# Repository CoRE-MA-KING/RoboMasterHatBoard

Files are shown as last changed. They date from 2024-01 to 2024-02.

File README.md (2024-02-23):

# RoboMasterHatBoard
ロボマス開発ボード用ハットです。  
CoREに出場するロボットに利用しているメインボードとして[RoboMaster 開発ボードタイプA](https://store.dji.com/jp/product/rm-development-board-type-a?vid=42041)を利用しているので、このボードから2024年大会用に必要なピンをコネクタにまとめるための基板です。

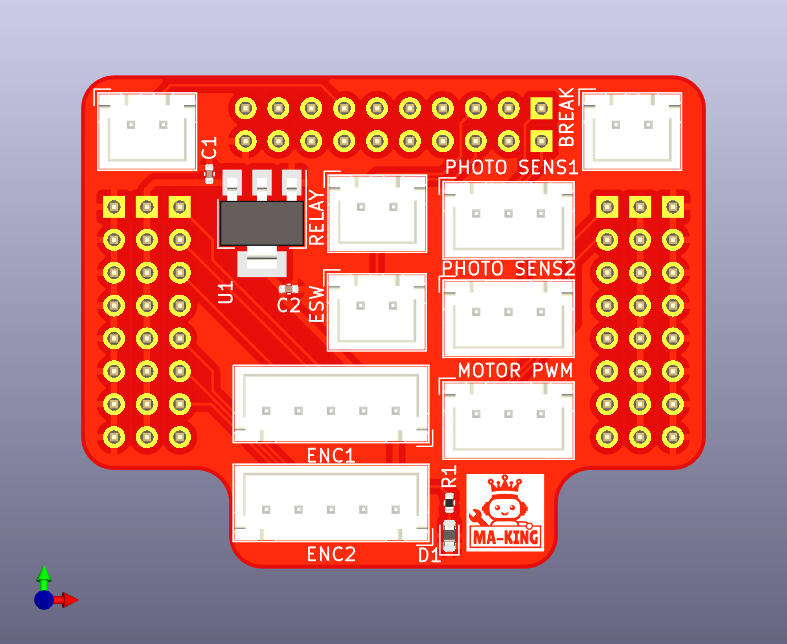
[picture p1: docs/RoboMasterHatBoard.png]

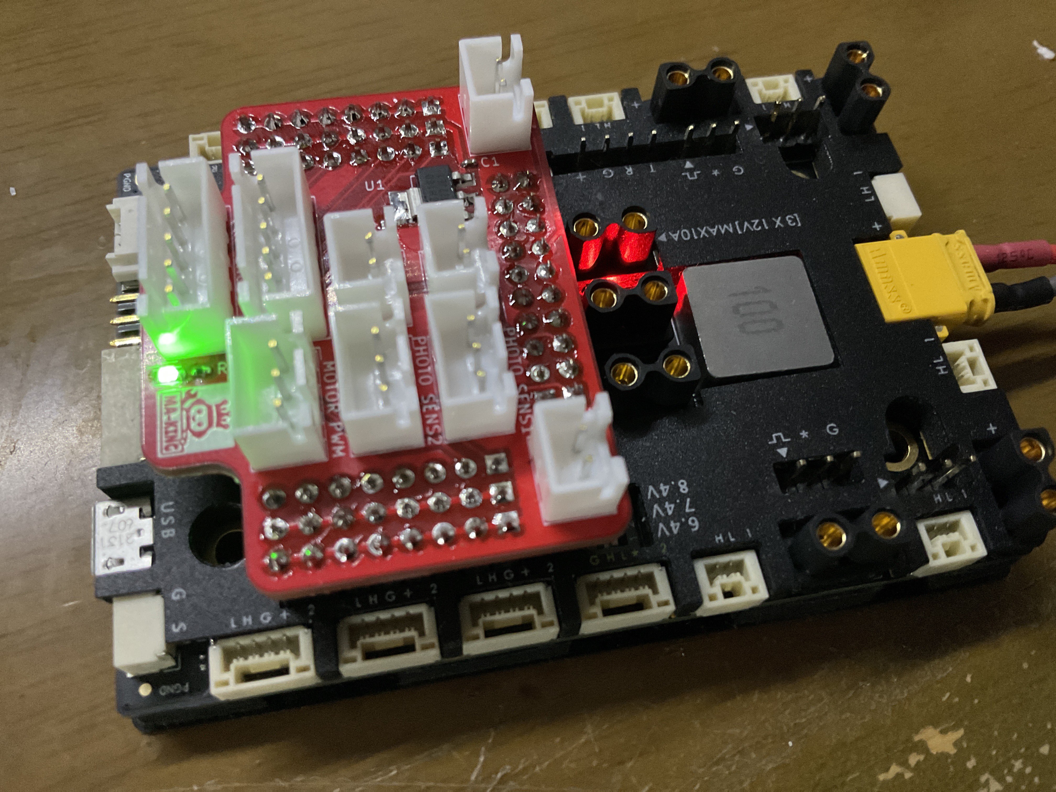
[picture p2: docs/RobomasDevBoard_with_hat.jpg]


# 機能
ロボマス開発ボードにはピンヘッダからいくつかのピンが出ているので、そこから今回のロボットで利用するピンを取り出します。

具体的に以下のピンを取り出します。
|ピン名|ペリフェラル|用途|備考|
|---|---|---|---|
|PD12|TIM4_CH1| モータ1PWM用||
|PD13|TIM4_CH2| モータ2PWM用||
|PA0|TIM2_CH1| エンコーダ1 A相||
|PA1|TIM2_CH2| エンコーダ1 B相||
|PA2|GPIO_INPUT| エンコーダ1 Z相||
|PI5|TIM8_CH1| エンコーダ2 A相||
|PI6|TIM8_CH2| エンコーダ2 B相||
|PI7|GPIO_INPUT| エンコーダ2 Z相||
|PF0|GPIO_INPUT|フォトインタラプタ1入力|マイコンの内部プルアップ必須|
|PF1|GPIO_INPUT|フォトインタラプタ2入力|マイコンの内部プルアップ必須|
|PE6|GPIO_INPUT|非常停止ボタン入力|マイコンの内部プルアップ必須|
|PE12|GPIO_OUTPUT|リレー駆動信号||
|PC3|GPIO_INPUT|撃破信号入力|PC3は5 Vトレラントなので5 V入力可能|
|PC1|GPIO|汎用GPIO|予備ポート 5 Vトレラントピン|

v0.1の基板上のシルクと回路図上の信号線が逆になっているので注意。回路図が間違っているということにして基板のシルクか上の表に従えばOK。

基板上のコネクタのピンアサインは次の通り
### MOTOR PWM
|1|2|3|
|---|---|---|
|TIM4_CH1(PD12)|TIM4_CH2(PD13)|GND|

### PHOTO SENS1
|1|2|3|
|---|---|---|
|5 V|INPUT(PF0)|GND|

### PHOTO SENS2
|1|2|3|
|---|---|---|
|5 V|INPUT(PF1)|GND|

### ENC1
|1|2|3|4|5|
|---|---|---|---|---|
|3.3 V|TIM2_CH1(PA1)|TIM2_CH2(PA2)|INPUT(PA2)|GND|

### ENC2
|1|2|3|4|5|
|---|---|---|---|---|
|3.3 V|TIM8_CH1(PI5)|TIM8_CH2(Pi6)|INPUT(PI7)|GND|

### RELAY
|1|2|
|---|---|
|OUTPUT(PE12)|GND|

### ESW
|1|2|
|---|---|
|INPUT(PE6)|GND|

### BREAK
|1|2|
|---|---|
|INPUT(PC3)|GND|

### 予備ポート
|1|2|
|---|---|
|INPUT(PC1)|GND|

## 参考
ロボマス開発ボードピンヘッダ部分のピンアサインは[回路図](https://ausdroid.co/wp-content/uploads/2020/08/RoboMaster-Development-Board-Type-A-Schematic.pdf)より
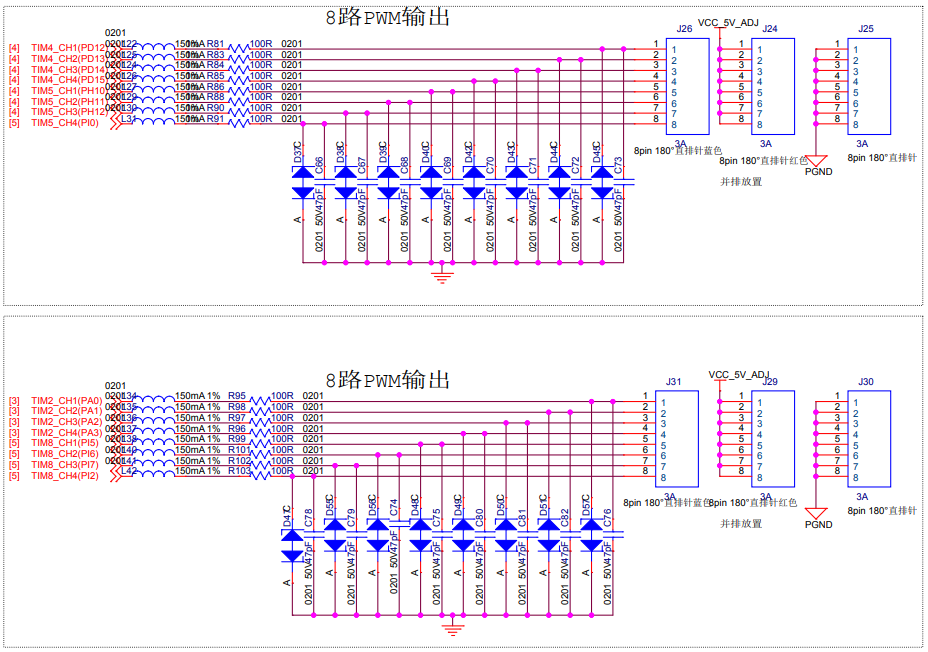
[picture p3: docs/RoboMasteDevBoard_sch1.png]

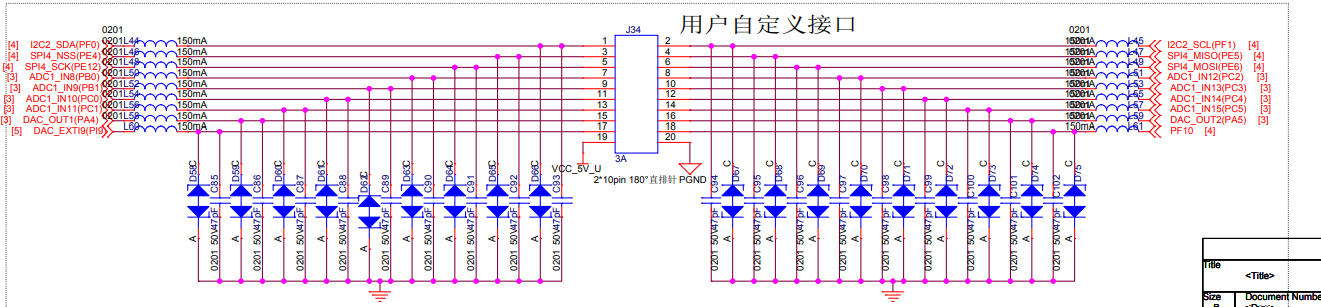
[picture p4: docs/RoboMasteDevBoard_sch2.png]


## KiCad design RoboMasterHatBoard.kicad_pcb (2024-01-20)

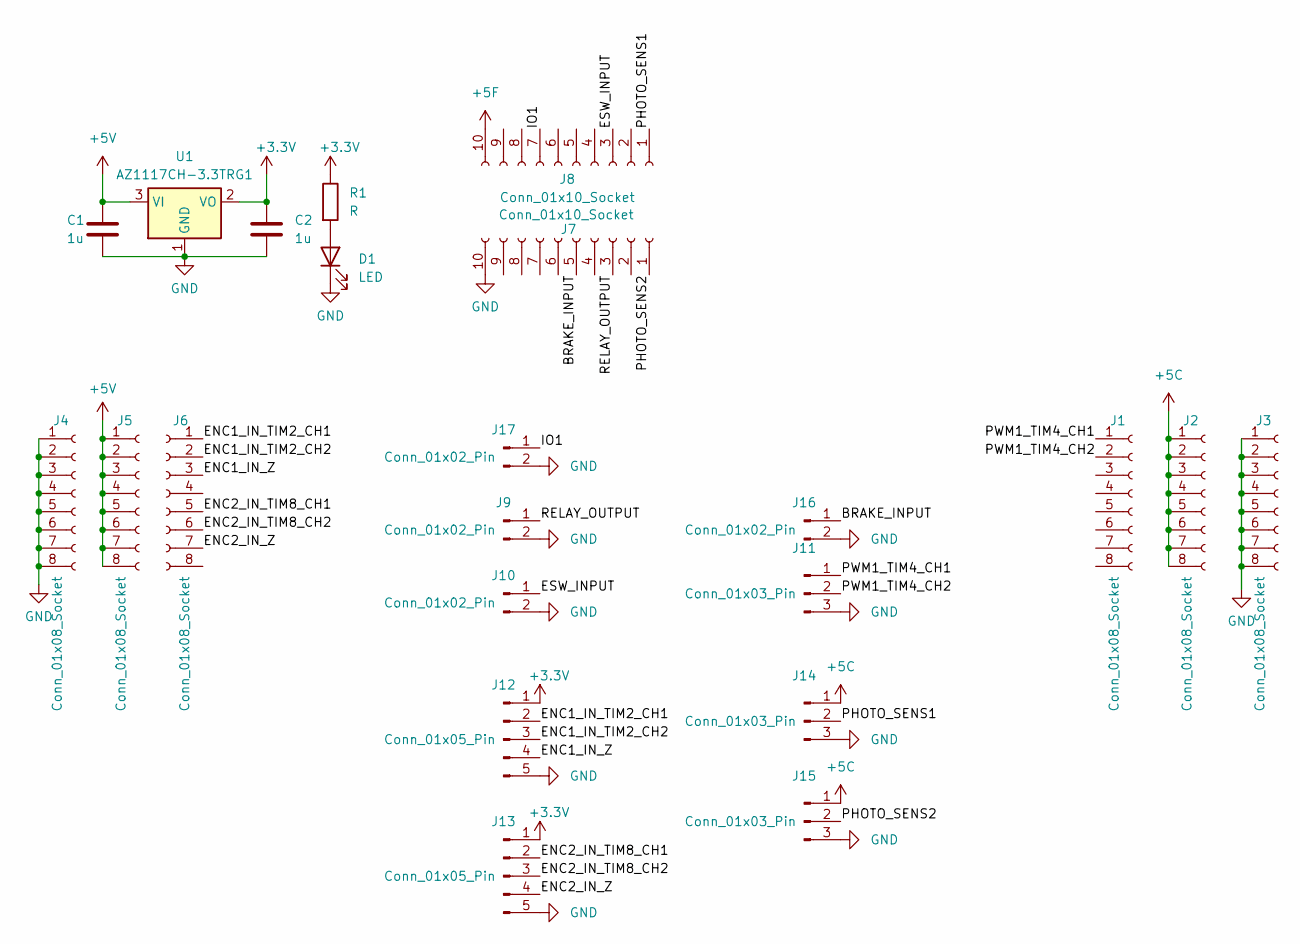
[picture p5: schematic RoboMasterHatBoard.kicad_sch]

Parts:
C1, C2: 1u; C_0402_1005Metric
D1: LED; D_0603_1608Metric
J1, J2, J3, J4, J5, J6: Conn_01x08_Socket; PinHeader_1x08_P2.54mm_Vertical
J7, J8: Conn_01x10_Socket; PinHeader_1x10_P2.54mm_Vertical
J9, J10, J16, J17: Conn_01x02_Pin; JST_XH_B2B-XH-A_1x02_P2.50mm_Vertical
J11, J14, J15: Conn_01x03_Pin; JST_XH_B3B-XH-A_1x03_P2.50mm_Vertical
J12, J13: Conn_01x05_Pin; JST_XH_B5B-XH-A_1x05_P2.50mm_Vertical
R1: R; R_0402_1005Metric
U1: AZ1117CH-3.3TRG1; SOT-223-3_TabPin2

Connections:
+3.3V: C2.1, J12.1, J13.1, R1.1, U1.2 (VO)
+5C: J2.1, J2.2, J2.3, J2.4, J2.5, J2.6, J2.7, J2.8, J14.1, J15.1
+5F: J8.10
+5V: C1.1, J5.1, J5.2, J5.3, J5.4, J5.5, J5.6, J5.7, J5.8, U1.3 (VI)
/BRAKE_INPUT: J7.5, J16.1
/ENC1_IN_TIM2_CH1: J6.1, J12.2
/ENC1_IN_TIM2_CH2: J6.2, J12.3
/ENC1_IN_Z: J6.3, J12.4
/ENC2_IN_TIM8_CH1: J6.5, J13.2
/ENC2_IN_TIM8_CH2: J6.6, J13.3
/ENC2_IN_Z: J6.7, J13.4
/ESW_INPUT: J8.3, J10.1
/IO1: J8.7, J17.1
/PHOTO_SENS1: J8.1, J14.2
/PHOTO_SENS2: J7.1, J15.2
/PWM1_TIM4_CH1: J1.1, J11.1
/PWM1_TIM4_CH2: J1.2, J11.2
/RELAY_OUTPUT: J7.3, J9.1
GND: C1.2, C2.2, D1.1 (K), J3.1, J3.2, J3.3, J3.4, J3.5, J3.6, J3.7, J3.8, J4.1, J4.2, J4.3, J4.4, J4.5, J4.6, J4.7, J4.8, J7.10, J9.2, J10.2, J11.3, J12.5, J13.5, J14.3, J15.3, J16.2, J17.2, U1.1 (GND)
unnamed: D1.2 (A), R1.2

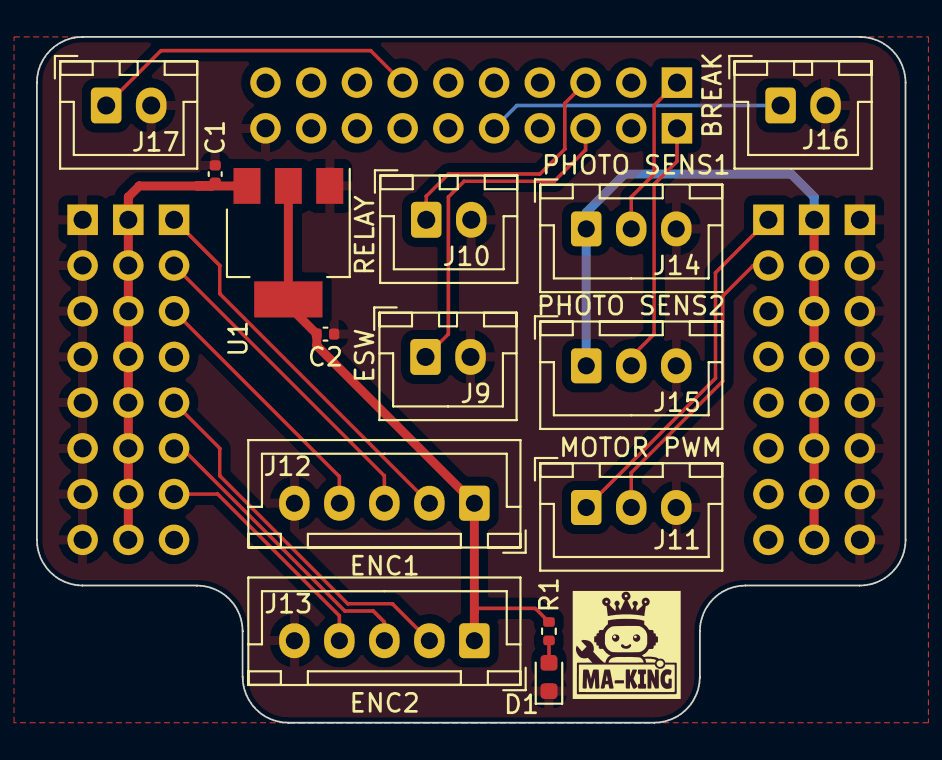
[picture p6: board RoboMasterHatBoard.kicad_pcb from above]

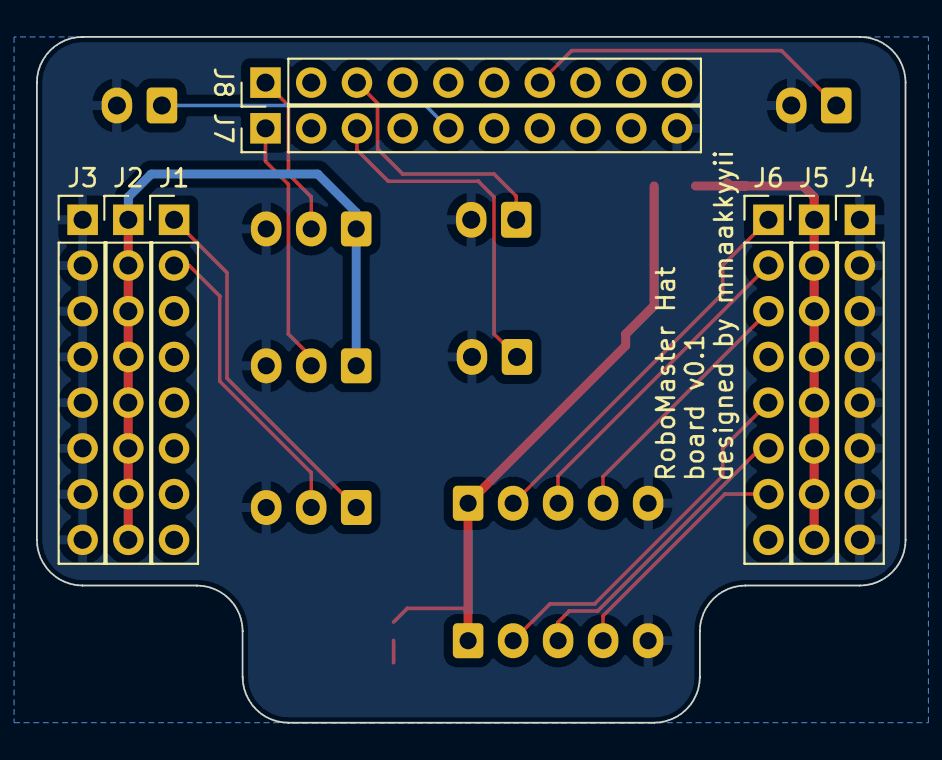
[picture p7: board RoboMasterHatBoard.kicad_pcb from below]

Board: 2 copper layers, 48.3 x 38.1 mm, 23 parts (8 on the bottom side), 19 nets.

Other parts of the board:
 : LOGO

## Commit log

2024-01-18 撃破入力ピンを追加
    [RoboMasterHatBoard.kicad_pcb, RoboMasterHatBoard.kicad_sch]
2024-01-20 add gerber
    [RoboMasterHatBoard-B_Cu.gbr, RoboMasterHatBoard-B_Mask.gbr, RoboMasterHatBoard-B_Paste.gbr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]
2024-02-21 readme追加
2024-02-21 ピンアサイン追記
2024-02-21 画像追加
